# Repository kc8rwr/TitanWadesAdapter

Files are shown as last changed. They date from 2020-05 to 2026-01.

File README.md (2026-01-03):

# BMG / Titan / Grove Mount to Wades Adapter

This is an adapter to attach an E3D Titan, Bondtech BMG or other compatible groove mount extruder to a Mendel90 or other carriage expecting a Wades extruder. This may work with other extruders/carriages with similar mounting styles. Many parameters may be changed, perhaps making it work with less similar printers and/or extruders. If you are only looking for a ready to print solution without customizing anything STLs are available on [Thingiverse](https://www.thingiverse.com/thing:4340787). The Thingiverse page also includes an STL for a modified Mendel90 d-motor mount allowing the original DB15 connector to be used with the new extruder.

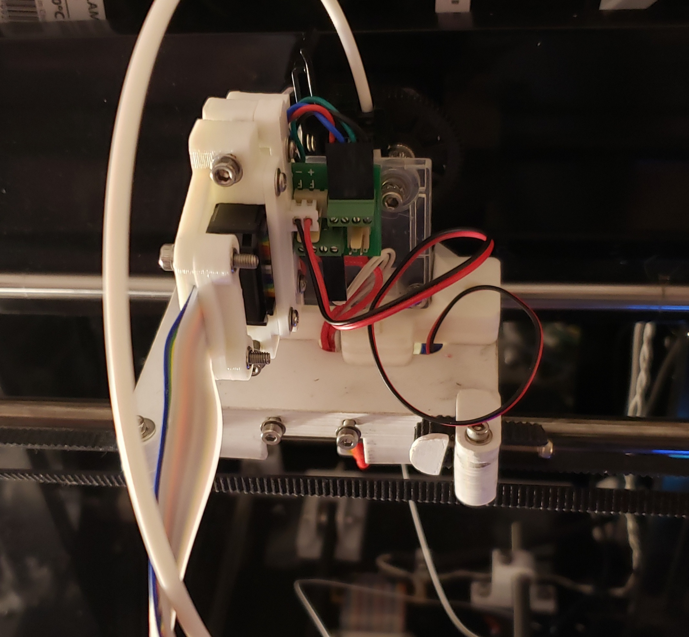
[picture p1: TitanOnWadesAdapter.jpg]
Titan


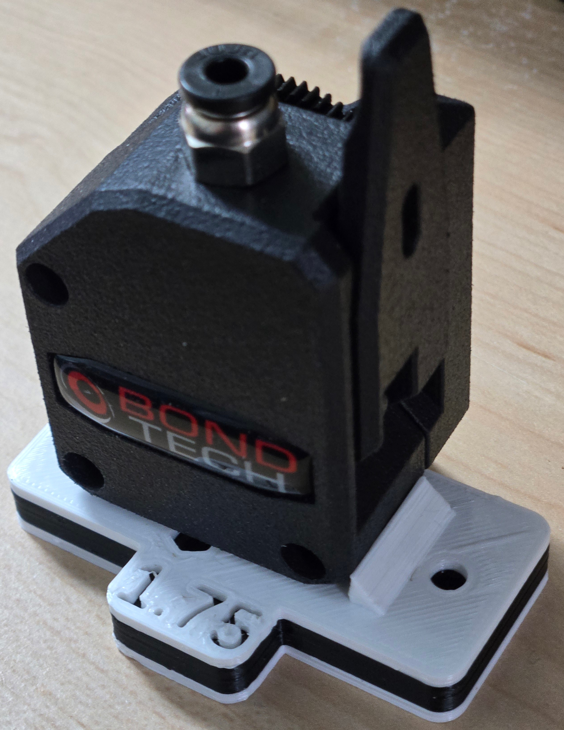
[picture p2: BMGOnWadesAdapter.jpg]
BMG


**Notes:**

* The hotend bolts to bottom of adapter just like with a Wades extruder. No additional groove mount bracket is necessary.
* The hotend attaches with 3 M3 bolts/washers as per the Wades design. Typically M3 washers are 7mm in diameter. This makes the heads of the bolts close to the hotend. That is not a problem with older J-head style hotends. It can make it hard to reach the bolts with an Allan wrench with newer hotends that have wider heat sinks. 9mm M3 washers are also available though less common. The bolt holes in the attached STLs are spaced for 9mm washers. This makes it a little easier to get a wrench in. 7mm washers might not extend far enough into the groove. Washer size is a configurable parameter in the scad file.
* One weakness of this design is that the length of the hotend bolts must be exact. If they are too long they will extend into the extruder.  With the default parameters 11mm is about the right length. 
* ~~Another is that the nuts are plain nuts. It remains to be seen if with use the hotend screws loosen. If they do then perhaps Loctite or Nylocs would work.~~<br/>**Update - after 2 years of use this has not been a problem.** I have avoided using Nylocs because that would require increasing the height of the bracket in order to make room for deeper nut wells.
* ~~I am using this with an all metal hotend that requires a fan. I did not want to run an extra wire for the fan. I am not using the probe connector on the PCB. Using a dremel I cut the trace between the probe connector and the thermistor ground. I then soldered a wire between that pin of the connector and the positive supply for the hotend and part cooling fan. At the other end of the ribbon cable I connected the wire that was supposed to be for the probe to ground. Then I connected the fan to what was supposed to be the probe connector and it is on whenever the printer is. This is not reflected in the first picture.~~<br/>**Update** - After upgrading my heater and motor electronics but not the fans to 24V the PCB hack is no longer sufficient. There is no additional conductor for a second positive voltage source.  Instead I just ran a couple fan extension wires alongside the ribbon, clamping them within the ribbon clamps. It's kind of messy but it works for now. I have not had any problems with crosstalk.

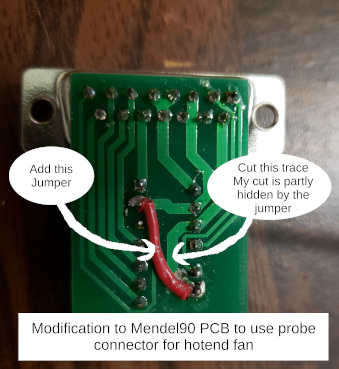
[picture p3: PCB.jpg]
PCB Modification


**Printing:**

* Designed not to require slicer generated supports
* A thin support shell for the groove mount which removes easily may be optionally generated
* A thin support skin may be printed across the filament hole so as to make the ceiling of the hotend mounting hole
  all bridge, no overhang.
* Optionally, the top and bottom halves may be generated separately, to be glued together later. Or just held together by
  the mounting bolts. This eliminates the bridging over the hotend mounting hole and may make a better interface to the hotend.

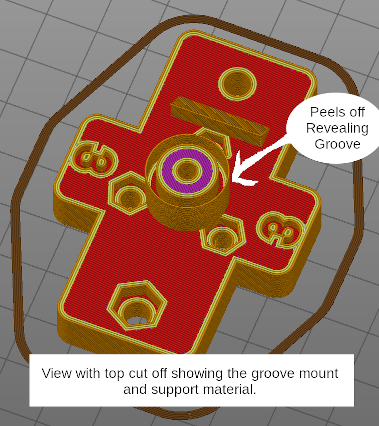
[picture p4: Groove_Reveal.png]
Groove Reveal


**This design was based on:**

* The adapter Thomas Sanladerer designed for his [review](https://toms3d.org/2016/04/24/review-e3d-titan-as-a-super-light-extruder/
) of the Titan. 
* [Wades Geared Extruder](https://reprap.org/wiki/Wade%27s_Geared_Extruder)
* [Bondtech BMG extruder](https://www.bondtech.se/product/bmg-extruder/)
* [E3D Titan](https://e3d-online.com/blogs/news/titan-the-lightweight-easy-to-use-extruder-from-e3d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) Discontinued but available as a clone
* And the [Mendel90](https://github.com/nophead/Mendel90) [RepRap](http://reprap.org)

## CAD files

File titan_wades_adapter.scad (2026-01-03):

/*
  Titan Wades Adapter

  Leif Burrow
  Unforgettability.net
  2020/05
  
  Parametric script to generate a 3d-model of an adapter for attaching a Titan or compatible extruder to
  a carriage which is designed for a Wades or similar extruder.

  This script was designed and tested for a Mendel90 Strudy variant.  Parameters may need adjustment for other printers.

  To avoid bridges or support in the hotend mount this model may be split between a top part and bottom part. For convenience
  the script can generate the top and bottom parts separately, divided in the best spot.

  The mounting bolts alone would probably hold everything together. I printed the part in ABS and used "ABS Juice" (ABS scraps
  disolved in acetone) to glue it together. Just apply a little ABS juice then quickly insert bolts with washers and nuts into
  each bolt hole and tighten them down to hold it together tightly while it dries.  If you are not inserting the small hotend
  bolts at this time be careful not to get any ABS Juice in the nut traps. The screw and filament holes may be easily drilled
  out if ABS gets in them but the hex shaped nut traps are not as easy to clear. I found that when ABS Juice squirted into
  the nut traps gently inserting a drill bit and twisting removed it without the pushing the sticky ABS against the nut trap walls.

  I printed two versions of this part, one for 3mm and one for 1.75mm filament. The goal was to build up two extruder/hotend
  assemblies which are identical in every  way except filament size so that they may be easily swapped as needed.  I have added
  optional front/back supports  which the original Wades extruder did not have. Besides potentially adding a little stability
  and support for the extruder motor these "cross supports" may be labeled using the "cross_support_label..." variables making
  it easy to identify which is which at a glance. Unfortunately OpenScad is not really aware of the size of text objects. This
  makes automatic positioning very difficult. I have included a couple of variables for moving the text in/out, left/right. If you
  change the text then adjust these parameters until it looks right.

  It would not do well to split the model in the middle of the hotend groove mount. That part must be strong. Therefore there is no
  way to print the top without having an overhang or support.  I have not had good luck using my slicer's generated supports. It has
  printed well enough without support that with some filing and sanding I could get the extruder to fit.  This still leaves it a bit
  "chewed up looking". What I have found works much better is to add a support shell around the outside of the groove as part of the
  model. If the thickness of this shell is set just right it prints perfectly yet is very easy to remove. The thickness of this shell
  is one of the settable parameters. Setting it to 0 to print without a shell.

  This mount uses 3 M3 screws, nuts and washers to hold the hotend just like a Wades extruder. This worked well with the older J-head
  hotends. I have found that newer hotends with metal heat sinks can done but it's kind of tricky to mount because the fins get in
  the way of the allen wrench. Using larger washers allows the bolts to be farther from the hotend making this easier. The typical
  washers for which Wades was designed are 7mm in diameter. The biggest I managed to find in M3 were 9mm. This only moves the bolt
  1mm farther out but even that seems to be enough to help.  Alternatively, if you would prefer to use the ordinary 7mm
  washers or if you have even larger ones there is a parameter for washer size. Just set it accordingly.

  Typically on a Mendel90 both mounting holes have traps for hex head bolts. The bolts extend downwards through the Wades extruder,
  through the carriage and are fastened under the carriage via wing nuts.  This works great with the older J-head hotends.
  Unfortunately newer hotends require fans on their heatsinks and this gets in the way of the bolt and wingnut.  The usual solution
  is to omit the hex trap on the right side and instead run the bolt on that side up from under the carriage and have the wingnut on top.
  The countersink_left_mount and countersink_right_mount parameters turn the left and right mounting bolt hex traps on/off respectively.

  The standard Mendel90 carriage also has hex traps on the bottom for the extruder mounting bolt holes. Another idea I might try is to
  glue nuts into these traps. Then I would trim a pair of thumbscrews to exactly the length necessary to bolt the extruder on without
  extending down into the fan area.  That way it would not be necessary to fumble around underneath the carriage to insert the bolt.

  Similarly, the nuts that hold the hotend are flush with the base of the adapter. The extruder must slide right over them. This means
  there cannot be any extra length to the bolts that hold the hotend on. They must fill the nut for stability but extend no farther
  when fully tightened. I did this mostly by trial and error with a cheap screw cutter.
  
  This model is contained within a module with many parameters. Custom versions may be generated by editing the call at the bottom
  of the file. Alternatively this file may be left unmodified by referencing this file within a second one via a use statement and
  calling the titan_wades_adapter() method with arguments.

  This program is free software: you can redistribute it and/or modify
  it under the terms of the GNU General Public License as published by
  the Free Software Foundation, either version 3 of the License, or
  (at your option) any later version.

  This program is distributed in the hope that it will be useful,
  but WITHOUT ANY WARRANTY; without even the implied warranty of
  MERCHANTABILITY or FITNESS FOR A PARTICULAR PURPOSE.  See the
  GNU General Public License for more details.

  You should have received a copy of the GNU General Public License
  along with this program.  If not, see <https://www.gnu.org/licenses/>.

*/

/* [Main] */

//the diameter of filament or ptfe liner tube to be used with this extruder
filament_diameter = 1.75;//[1.75, 2.85, 3, 4, 6.25]

//total width (left/right) of the adapter
width = 66;

//depth (front/back) of the adapter, not counting front/back cross supports
depth = 28;

//thickness up/down of the base of the adapter (note - if the top and bottom are printed separately it must be thick enough to include top and bottom nut traps with space in between
thickness = 9;

//generate the top part, the bottom part or the whole model
side = "both"; // [top,bottom,both]

/* [Hotend Mount] */

//the diameter of the hotend hole
hotend_diameter = 16;

//height of the lip at the top of the hotend (distance from groove to top)
hotend_lip_height = 4;

//how deep into the hotend is the groove at the top
hotend_groove_depth = 2;

//the diameter of the wide part of the hotend hole
extruder_diameter = 16;

//the height of the groove
extruder_lip_height = 3.5;

//nut trap diameter for the hotend mount
hot_nut_diameter = 6.5;

//thickness of a hotend nut, dept of the nut trap
hot_nut_height = 2.4;

//diameter of the hotend bolts
hot_bolt_diameter = 3.2;

//diameter of the hotend mounting washers
washer_diameter = 9;

/* [Extruder Mount] */

//distance between the center of the filament hole and the wedge which keeps the extruder from spinning around it's mount. Change for mounting a different width of extruder.
extruder_stop = 14;//[5:0.25:20]

//distance between the top of the adapter base and the bottom of the groove in the extruder mount
extruder_groove_raise = 4;

//how deep the extruder mount groove goes towards the filament hole
extruder_groove_depth = 2;

//how tall is the extruder mount grove
extruder_groove_height = 6;

//the thickness of the extruder lip support. It should be just thick enough to print cleanly yet be easy to remove. A value of 0.6 worked well for me but this may vary.
extruder_lip_support = 0.6;

//print a skin this thick across the filament hole right at the top of the extruder mounting hole. For single-piece printing, this allows the printer to bridge across the hole rather than stopping in mid-air at the center. It may be easily drilled out for use.
filament_hole_support_skin = 0.5;

/* [Carriage Mount] */

//should the left-hand mounting bolt hole include a trap for the head at top
countersink_left_mount = true; // [true,false]

//if there is a trap on the left is it hex vs round
mount_bolt_hex_left = true; // [true,false]

//should the right-hand mounting bolt hole include a trap for the head at top
countersink_right_mount = false; // [true, false]

//if there is a trap on the right is it hex vs round
mount_bolt_hex_right = false; // [true,false]

//how far apart are the mounting holes
mount_bolt_spacing = 50;

//diameter of the mounting holes
mount_bolt_diameter = 4.5;

//head diameter for round headed mounting bolts
mount_bolt_head_diameter = 7.5;
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

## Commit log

2026-01-03 Added support skin for hotend hole ceiling across the filament hole. Added filament hole diameters for using PTFE tubes.
    [titan_wades_adapter.scad]
2026-01-03 Added json with presets for both E3D Titan and Bondtech BMG extruders.
2026-01-03 Added image with BMG extruder.
